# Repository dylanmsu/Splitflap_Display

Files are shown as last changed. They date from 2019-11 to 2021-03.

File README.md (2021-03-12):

# Splitflap_Display
software to digtally drive a public splitflap display using arduino. The display is meant do be deployed in a steamtrain station where it reads the data from their server.
This project is still in development and requires major improvements and code cleanup.

## this repository contains:
* arduino library
* kicad schematic and pcb desgin
* basic documentation about the splitflap display modules

## The Arduino compatible Library
The included Arduino compatible library is designed to drive a complete split flap display board with 32 individual modules. There are also methods included to drive the individual split flaps with great control. You can for example call the method:
```c++
splitflaps.flipSegment(int segment);
```
That line of code will flip the segment once. Or if you want more control, there is the method: 
```c++
splitflaps.writeSegment(int segment, int state);
```
It sets the state of the selected h-Bridge. There are (in the future) a bunch of example sketches with different use cases for the library. However, they all require at least one driver PCB to actually drive the split flap modules.

## The driver PCB
The driver PCBs can drive 8 splitflap modules at the same time, for that it uses 4 SN754410NE chips (L293D in version 4) that are driven by two 74HC595 shift registers. One shift registers drives the H-bridges, the other enables the outputs of the 8 H-Bridges so they dont waste unnecessary power. The communication protocol is quite simple. You have two serial data inputs in the input connector, one is to enable the individual H-Bridges (DiE, ClkE, LaE), the other is to drive the individual H-bridges (Di, Clk, La). They can be daisy-chained to drive an infinite number of splitflap modules. <br> To actually drive splitflap modules with it, open the arduino sketch named TestDriver. Connect the splitflap modules solenoid connections to the H-Bridge output pairs. Then connect the serial pins to the arduino pins listed in the sketch. and lastly connect 20v to the Vdd input connector. Upload the sketch, the splitflaps should be working.

* V1: first version, fully made in kicad with through hole components
* V4: latest version, made in EasyEDA with mostly SMD components

## authors
* Dylan Missuwe
* Tijl Desmet

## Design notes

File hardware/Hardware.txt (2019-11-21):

SEEIT SMTRELAY04 Relaismodule
https://www.conrad.be/p/seeit-smtrelay04-relaismodule-095841
€ 10,49 OK

Highlights
Relaiskaart
4 relais-uitgangen
Compatible met 5V boards

Uitvoering
4 relais-uitgangen
Direct aan te sturen via 5V/DC signaal
Schakelspanning/stroom 250 V/AC 10 A
Eenvoudig aan te sluiten via schroefklemmen
Statusweergave via rode LED.

Netgear GS305E-100PES
https://www.coolblue.be/nl/product/831149/netgear-gs305e-100pes.html
39  € OK

EnGenius ENS202EXTv2
Outdoor 2,4GHz 11n Access Point
€ 102,85 OK

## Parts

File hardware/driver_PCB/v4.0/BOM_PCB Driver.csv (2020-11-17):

ID | Name | Designator | Footprint | Quantity | Manufacturer Part | Manufacturer | Supplier | Supplier Part | LCSC Assembly
1 | CD4049UBDR | U1,U2 | SOIC-16_L9.9-W3.9-P1.27-LS6.0-BL | 2 | CD4049UBDR | TI | LCSC | C22429 | Yes
2 | 100uF | C10,C9,C12,C11 | CAP-TH_BD6.3-P2.50-D1.0-FD | 4 | 100uF 35V 6.3*11 | ValuePro | LCSC | C19504
3 | 10uF | C5,C2,C3,C4,C8,C6,C7,C1 | C0805 | 8 | CL21A106KAYNNNE | SAMSUNG | LCSC | C15850 | Yes
4 | 74HC595D,118 | U3,U4 | SOIC-16_L9.9-W3.9-P1.27-LS6.0-BL | 2 | 74HC595D,118 | Nexperia | LCSC | C5947 | Yes
5 | L293DD013TR | U7,U8,U6,U5 | SOP-20_L13.2-W7.8-P1.27-LS10.4-BL | 4 | L293DD013TR | STMicroelectronics | LCSC | C21610 | Yes
6 | WJ127-5.0-4P | J1,J4,J3,J2 | CONN-TH_4P-P5.00_WJ127-5.0-4P | 4 | WJ127-5.0-4P | Ningbo Kangnex Elec | LCSC | C192779
7 | Shenzhen | CN2,CN1 | CONN-TH_12P-P2.54_B-3100R12P-A110 | 2 | B-3100R12P-A110 | Shenzhen Cankemeng | LCSC | C383583
8 | DB104S | D7,D5,D2,D8,D3,D6,D4,D1 | DBS_L8.4-W6.4-P5.10-LS10.2-TL | 8 | DB104S | MDD | LCSC | C38024 | Yes
9 | JL127-50802G01 | U9 | CONN-TH_2P-P5.08_JL127-50802G01 | 1 | JL127-50802G01 | JILN | LCSC | C409161

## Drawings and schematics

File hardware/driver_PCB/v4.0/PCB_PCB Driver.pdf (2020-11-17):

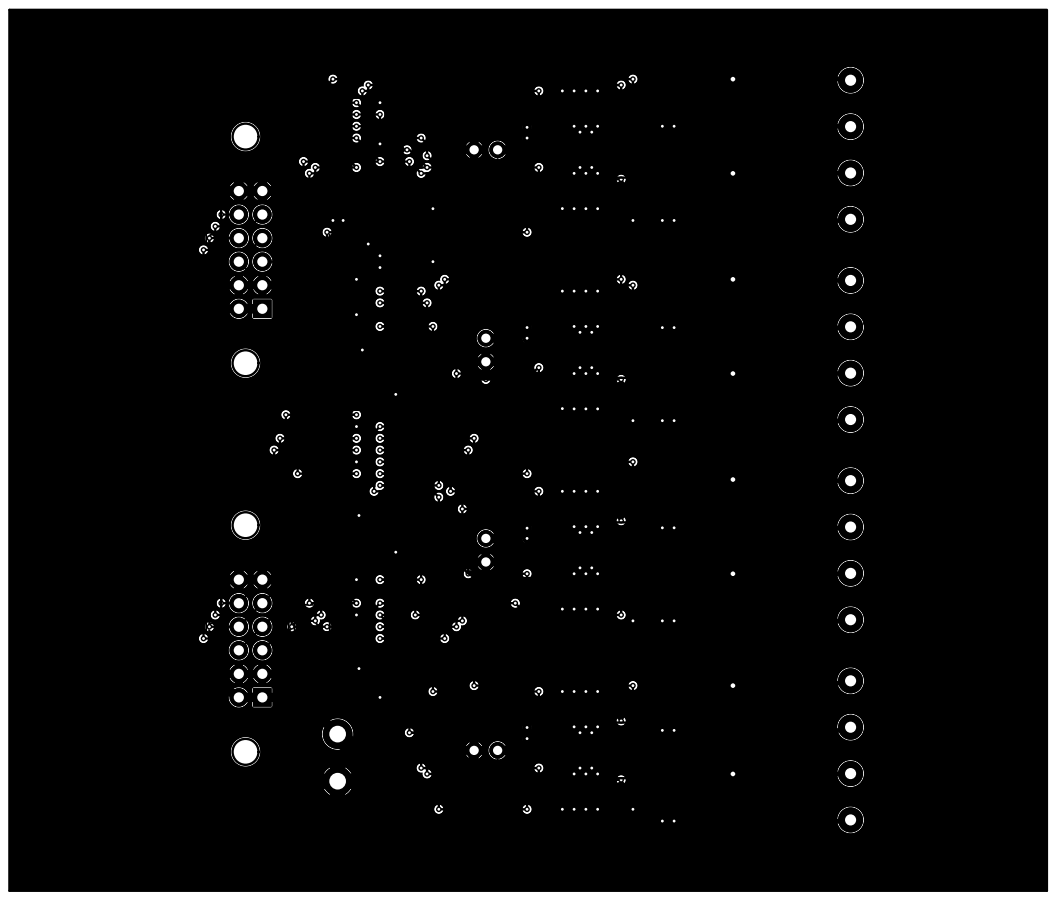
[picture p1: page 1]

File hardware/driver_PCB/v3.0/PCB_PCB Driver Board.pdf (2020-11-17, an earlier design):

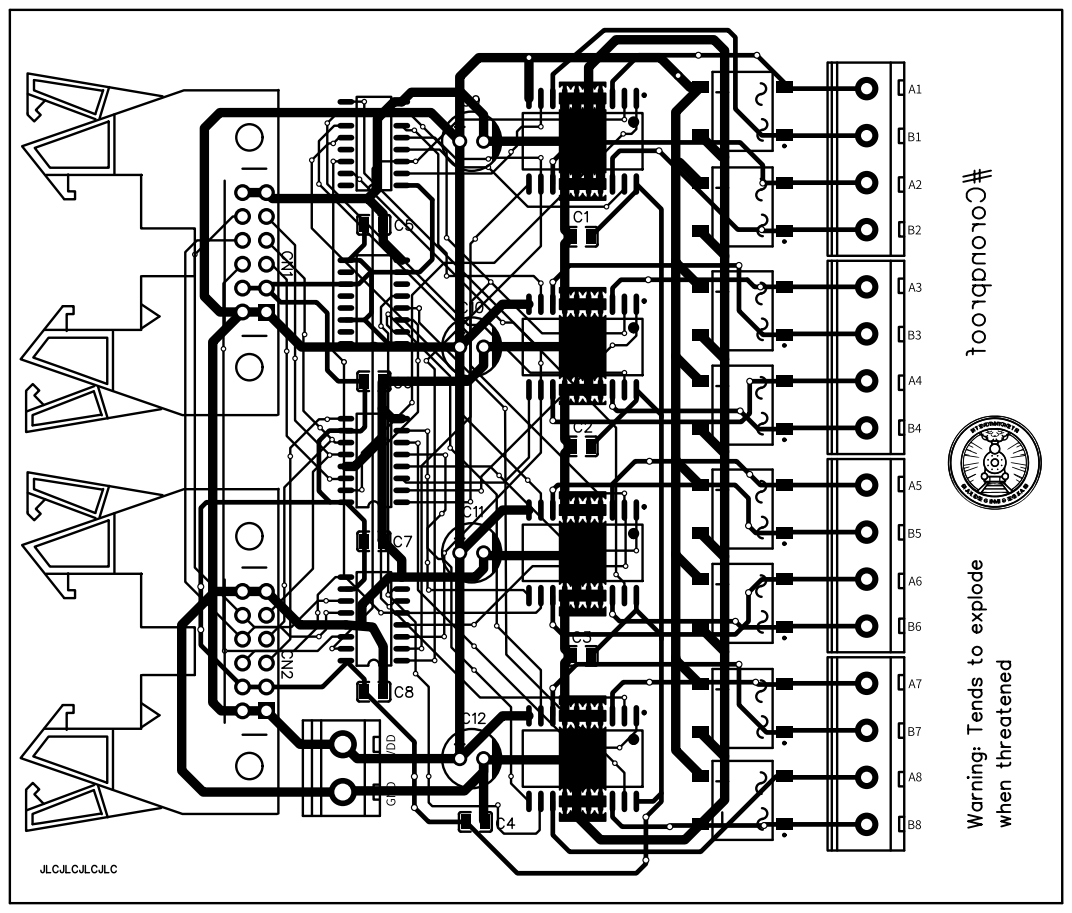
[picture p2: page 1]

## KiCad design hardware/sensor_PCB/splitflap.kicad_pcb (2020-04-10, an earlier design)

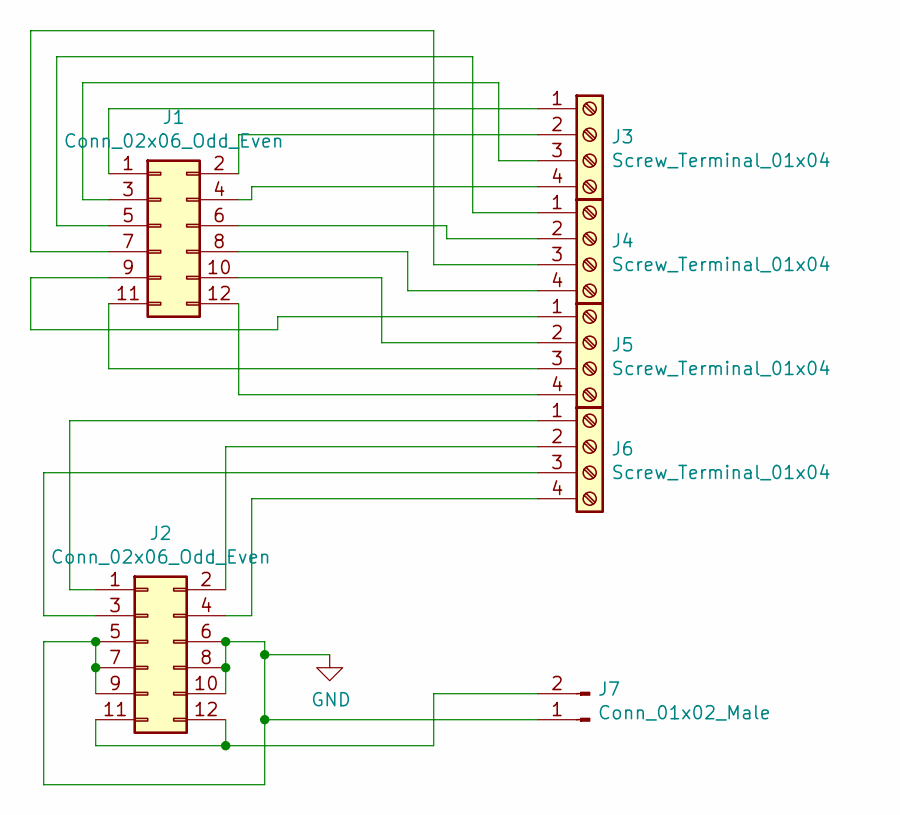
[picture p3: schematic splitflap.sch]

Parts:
J1, J2: Conn_02x06_Odd_Even; IDC-Header_2x06_P2.54mm_Vertical
J3, J4, J5, J6: Screw_Terminal_01x04; TerminalBlock_bornier-4_P5.08mm
J7: Conn_01x02_Male; JST_EH_B2B-EH-A_1x02_P2.50mm_Vertical

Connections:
GND: J2.5, J2.6, J2.7, J2.8, J2.9, J2.10, J7.1
unnamed: J1.1, J3.1
unnamed: J1.2, J3.2
unnamed: J1.3, J3.3
unnamed: J1.4, J3.4
unnamed: J1.5, J4.1
unnamed: J1.6, J4.2
unnamed: J1.7, J4.3
unnamed: J1.8, J4.4
unnamed: J1.9, J5.1
unnamed: J1.10, J5.2
unnamed: J1.11, J5.3
unnamed: J1.12, J5.4
unnamed: J2.1, J6.1
unnamed: J2.2, J6.2
unnamed: J2.3, J6.3
unnamed: J2.4, J6.4
unnamed: J2.11, J2.12, J7.2

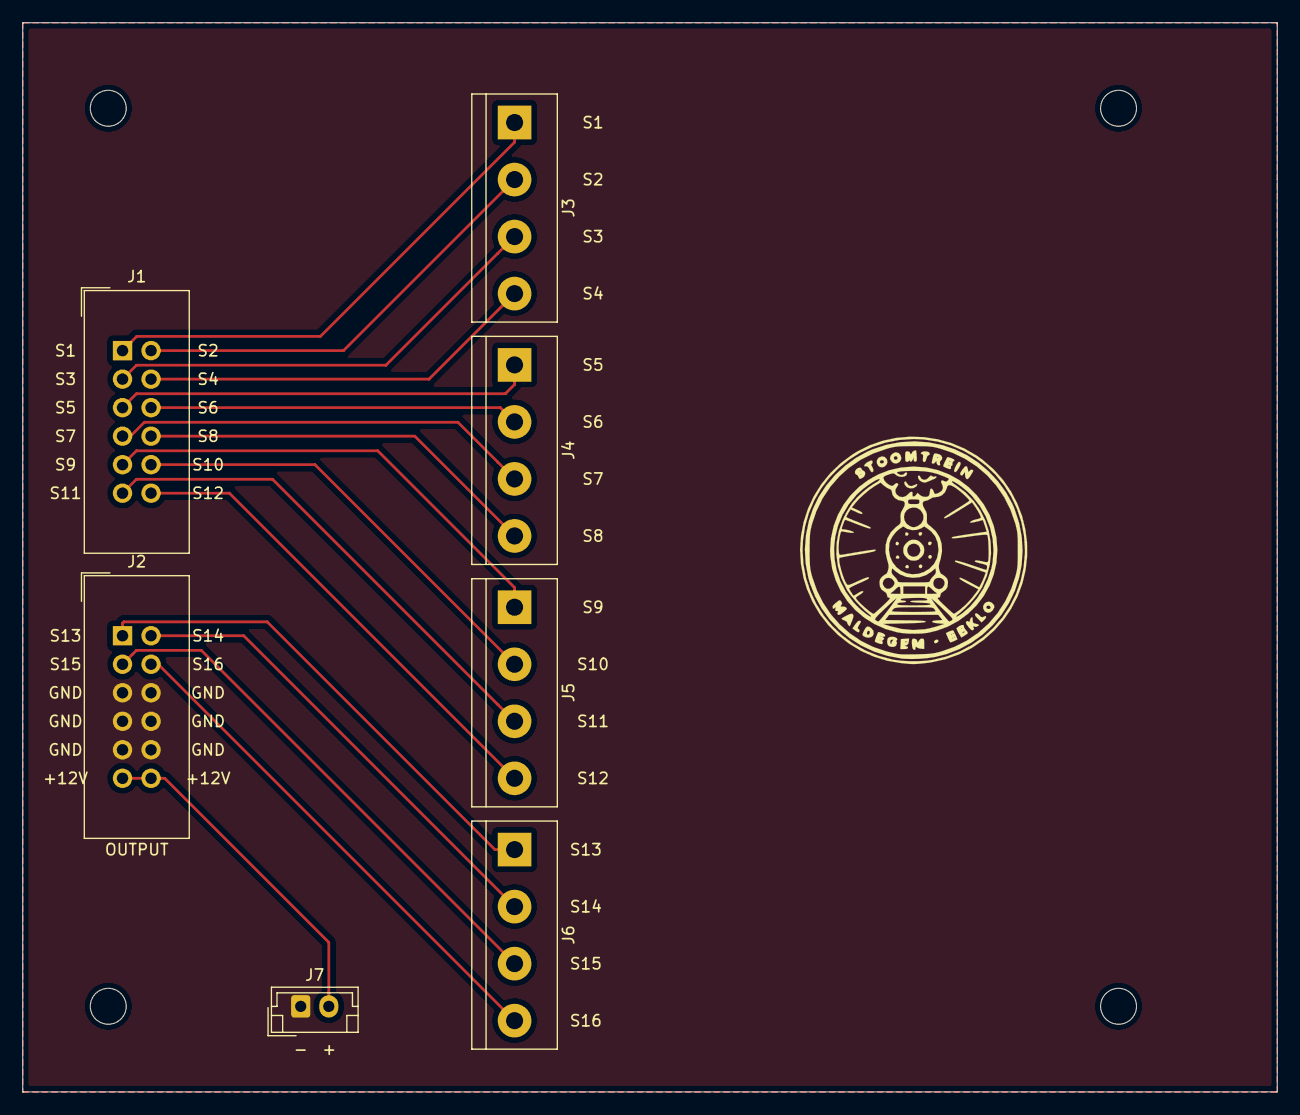
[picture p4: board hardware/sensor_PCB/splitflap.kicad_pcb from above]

Board: 2 copper layers, 111.8 x 95.2 mm, 7 parts (0 on the bottom side), 18 nets.

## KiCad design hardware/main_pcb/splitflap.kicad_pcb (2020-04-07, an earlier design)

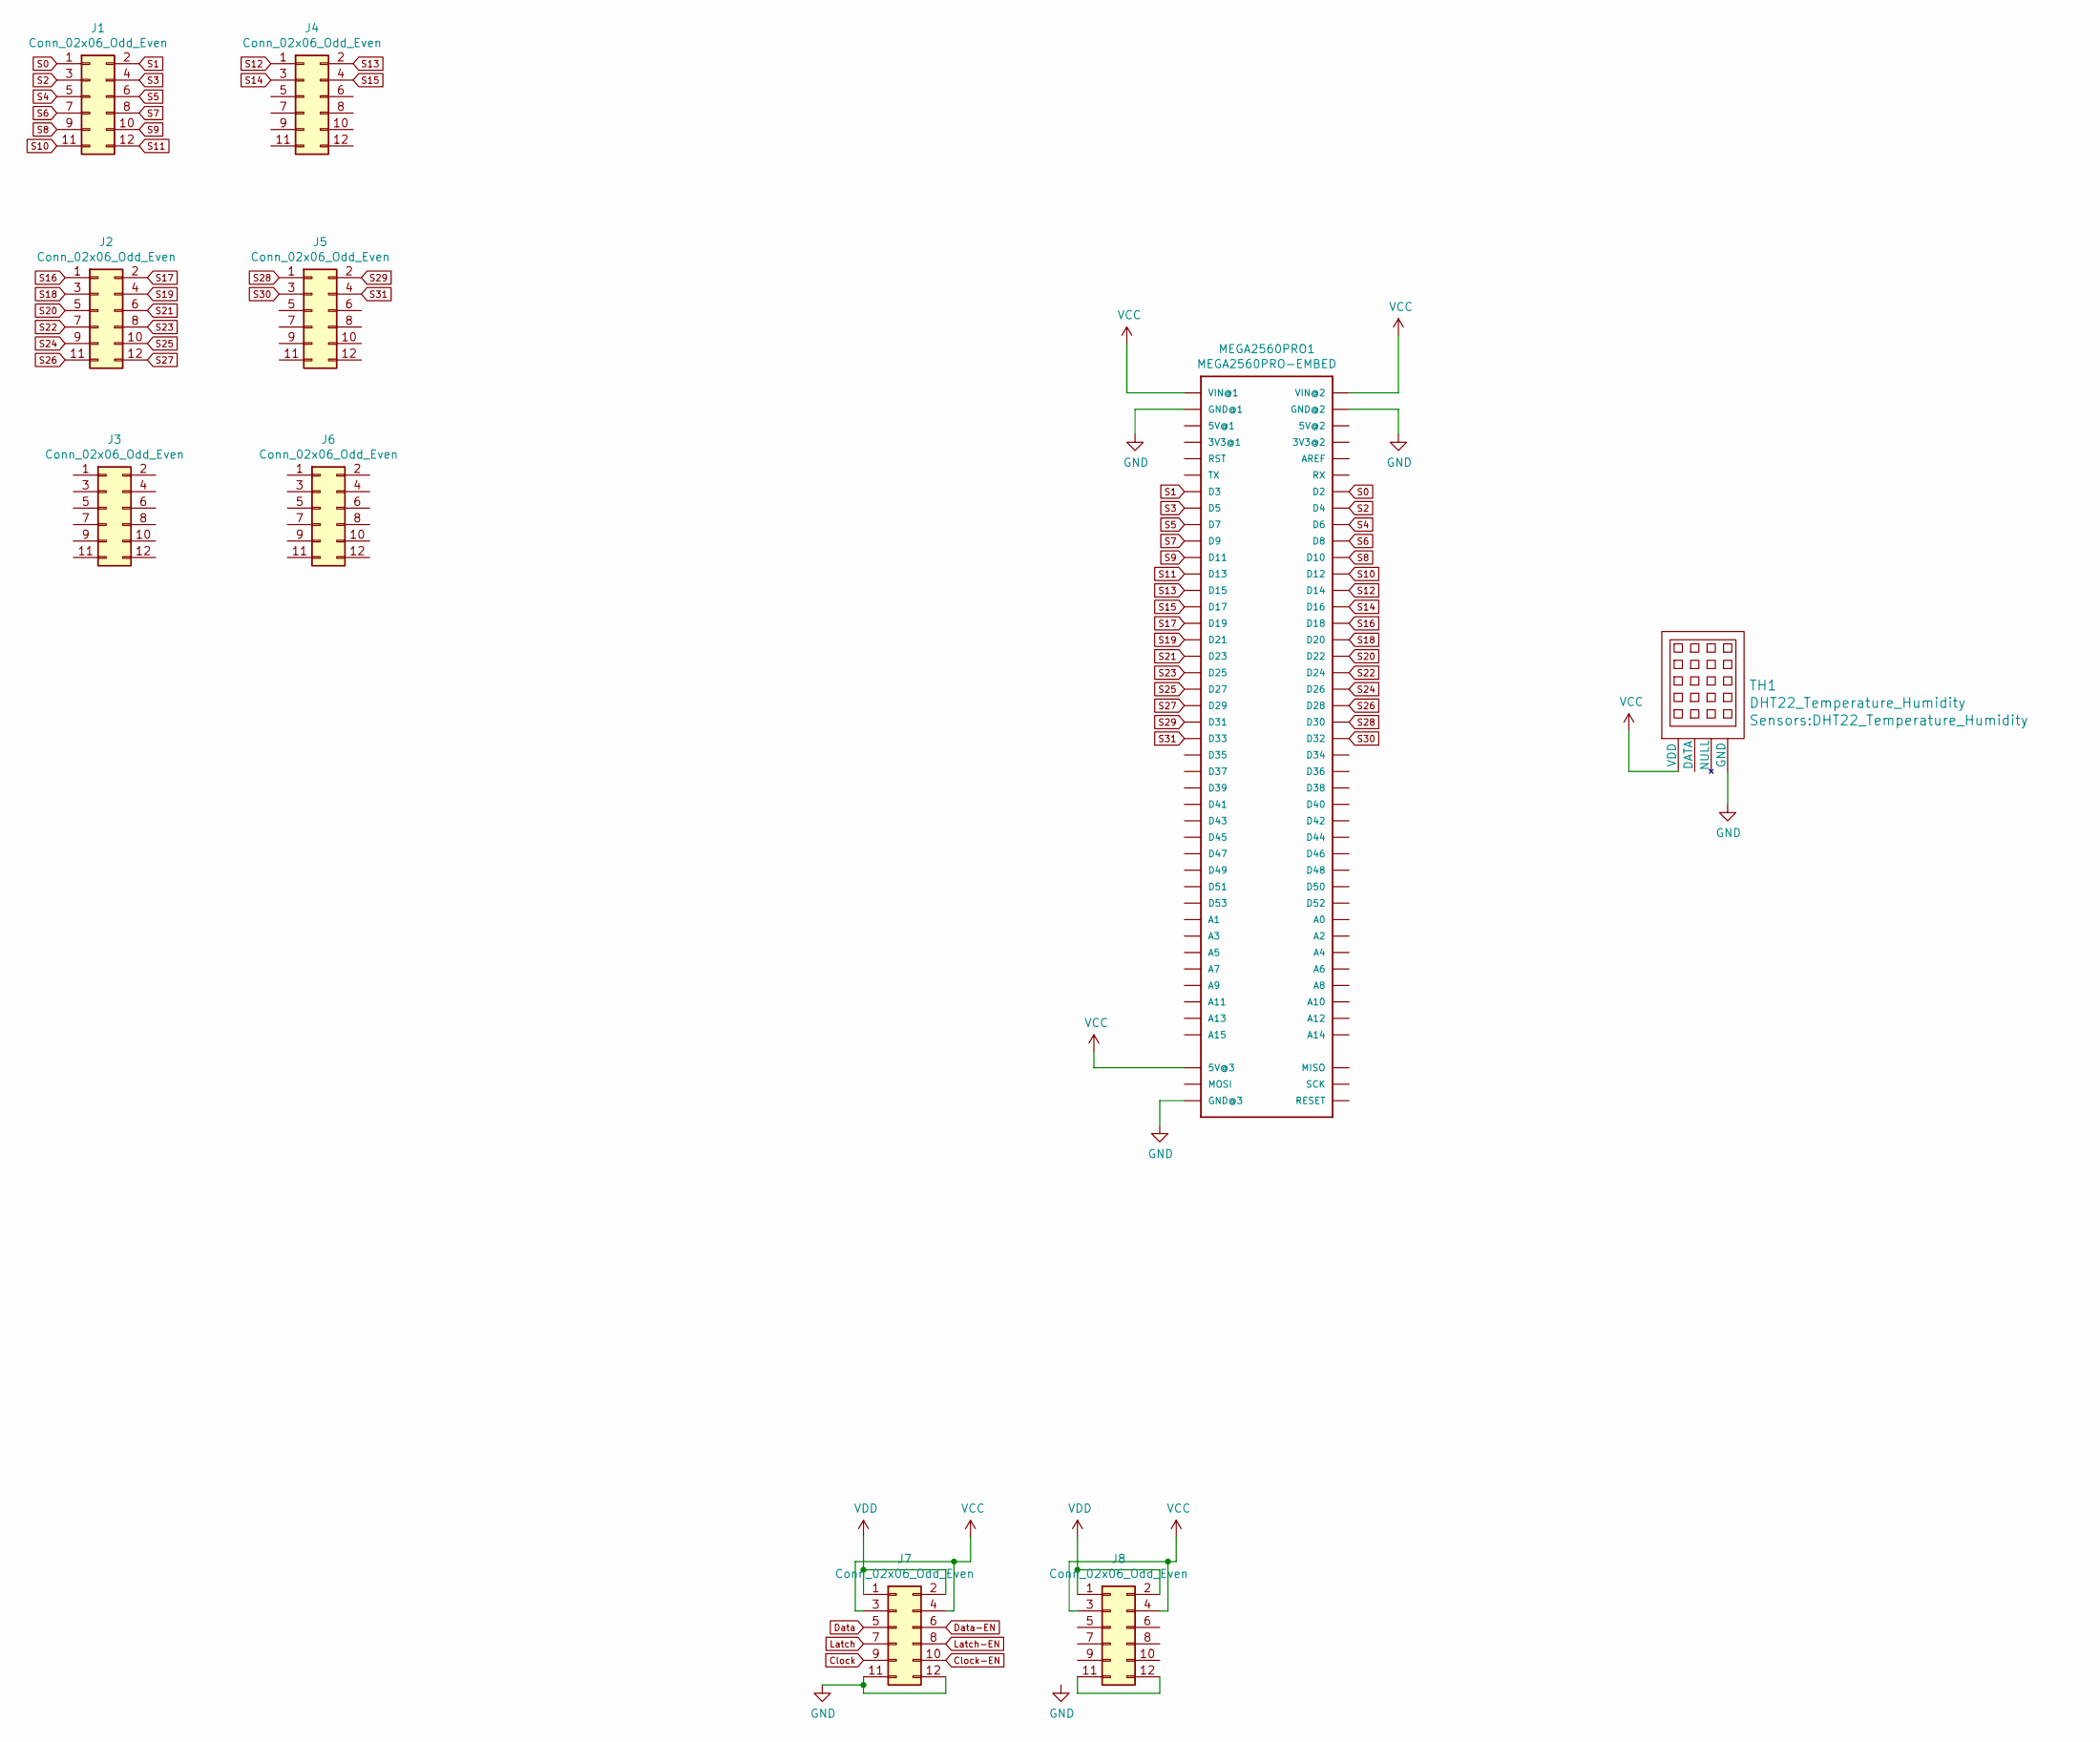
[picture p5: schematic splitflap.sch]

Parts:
J1, J2, J3, J4, J5, J6, J7, J8: Conn_02x06_Odd_Even; IDC-Header_2x06_P2.54mm_Vertical
MEGA2560PRO1: MEGA2560PRO-EMBED
TH1: DHT22_Temperature_Humidity

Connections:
Clock: J7.9
Clock-EN: J7.10
Data: J7.5
Data-EN: J7.6
GND: J7.11, J7.12, MEGA2560PRO1.GND@1, MEGA2560PRO1.GND@2, MEGA2560PRO1.GND@3, TH1.4 (GND)
Latch: J7.7
Latch-EN: J7.8
unnamed: J8.11, J8.12
S0: J1.1, MEGA2560PRO1.D2
S1: J1.2, MEGA2560PRO1.D3
S2: J1.3, MEGA2560PRO1.D4
S3: J1.4, MEGA2560PRO1.D5
S4: J1.5, MEGA2560PRO1.D6
S5: J1.6, MEGA2560PRO1.D7
S6: J1.7, MEGA2560PRO1.D8
S7: J1.8, MEGA2560PRO1.D9
S8: J1.9, MEGA2560PRO1.D10
S9: J1.10, MEGA2560PRO1.D11
S10: J1.11, MEGA2560PRO1.D12
S11: J1.12, MEGA2560PRO1.D13
S12: J4.1, MEGA2560PRO1.D14
S13: J4.2, MEGA2560PRO1.D15
S14: J4.3, MEGA2560PRO1.D16
S15: J4.4, MEGA2560PRO1.D17
S16: J2.1, MEGA2560PRO1.D18
S17: J2.2, MEGA2560PRO1.D19
S18: J2.3, MEGA2560PRO1.D20
S19: J2.4, MEGA2560PRO1.D21
S20: J2.5, MEGA2560PRO1.D22
S21: J2.6, MEGA2560PRO1.D23
S22: J2.7, MEGA2560PRO1.D24
S23: J2.8, MEGA2560PRO1.D25
S24: J2.9, MEGA2560PRO1.D26
S25: J2.10, MEGA2560PRO1.D27
S26: J2.11, MEGA2560PRO1.D28
S27: J2.12, MEGA2560PRO1.D29
S28: J5.1, MEGA2560PRO1.D30
S29: J5.2, MEGA2560PRO1.D31
S30: J5.3, MEGA2560PRO1.D32
S31: J5.4, MEGA2560PRO1.D33
VCC: J7.3, J7.4, J8.3, J8.4, MEGA2560PRO1.5V@3, MEGA2560PRO1.VIN@1, MEGA2560PRO1.VIN@2, TH1.1 (VDD)
VDD: J7.1, J7.2, J8.1, J8.2

Board: 2 copper layers, 10 parts (0 on the bottom side), 36 nets, no tracks yet.

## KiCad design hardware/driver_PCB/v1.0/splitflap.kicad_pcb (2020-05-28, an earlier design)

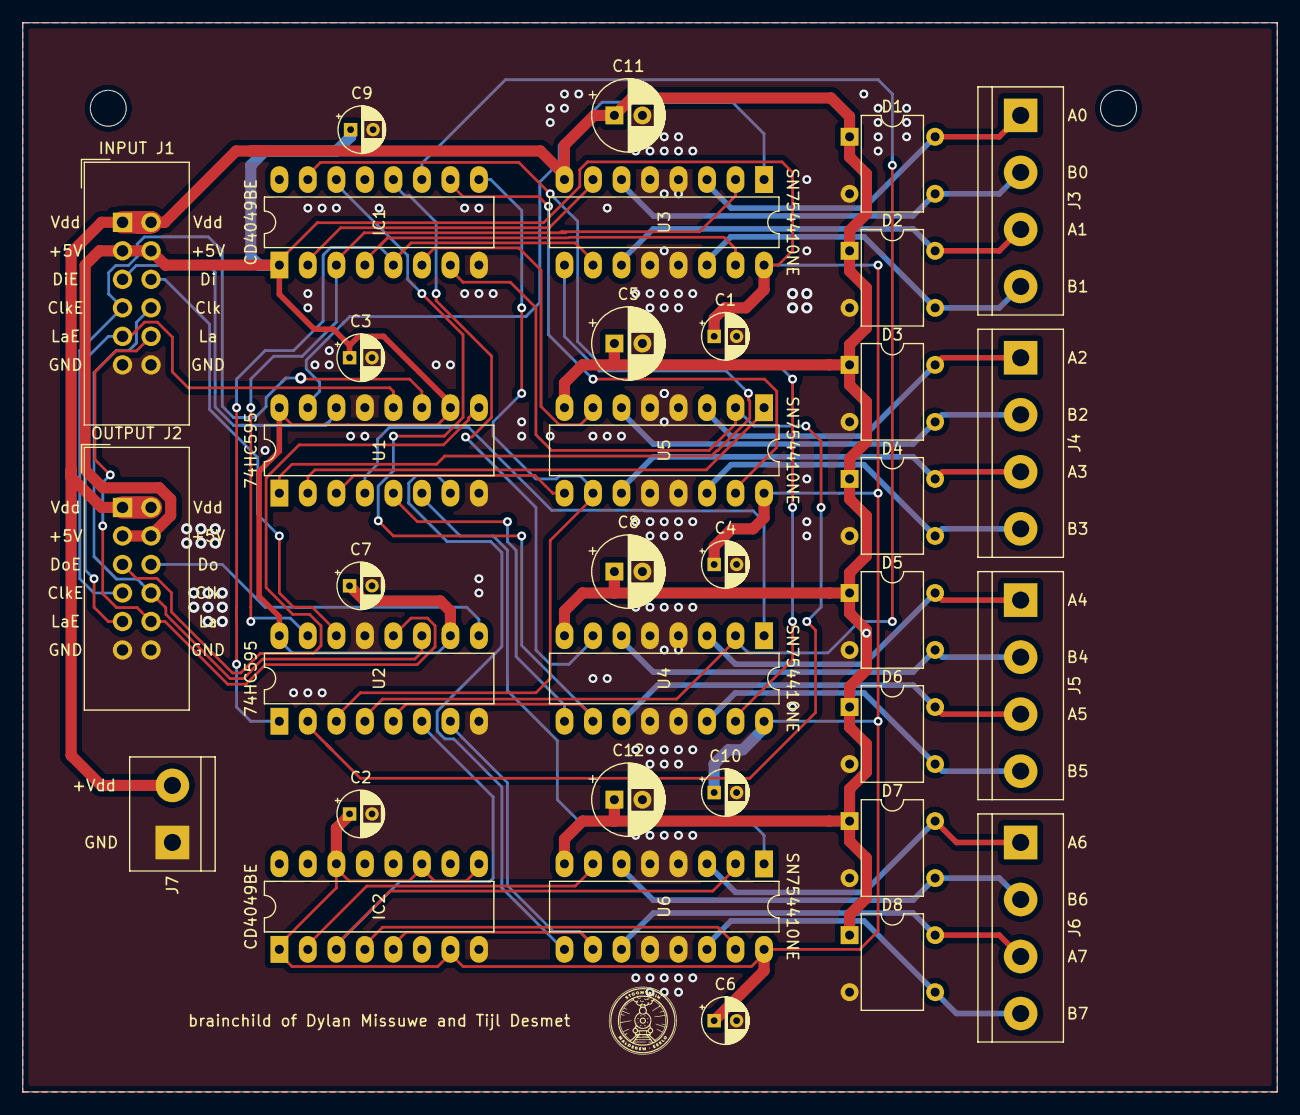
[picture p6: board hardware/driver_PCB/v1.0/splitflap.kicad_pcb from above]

Board: 2 copper layers, 111.8 x 95.2 mm, 35 parts (0 on the bottom side), 51 nets.

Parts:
C1, C2, C3, C4, C6, C7, C9, C10: CP; CP_Radial_D4.0mm_P2.00mm
C5, C8, C11, C12: CP; CP_Radial_D6.3mm_P2.50mm
D1, D2, D3, D4, D5, D6, D7, D8: D_Bridge_+-AA; Diode_Bridge_DIP-4_W7.62mm_P5.08mm
IC1, IC2: CD4049UBE; DIP-16_W7.62mm_LongPads
INPUT J1: Conn_02x06_Odd_Even; IDC-Header_2x06_P2.54mm_Vertical
J3, J4, J5, J6: Screw_Terminal_01x04; TerminalBlock_bornier-4_P5.08mm
J7: Screw_Terminal_01x02; TerminalBlock_bornier-2_P5.08mm
OUTPUT J2: Conn_02x06_Odd_Even; IDC-Header_2x06_P2.54mm_Vertical
U1, U2: 74HC595; DIP-16_W7.62mm_LongPads
U3, U4, U5, U6: SN754410NE; DIP-16_W7.62mm_LongPads

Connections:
GND: C1.2, C2.2, C3.2, C4.2, C5.2, C6.2, C7.2, C8.2, C9.2, C10.2, C11.2, C12.2, D1.2, D2.2, D3.2, D4.2, D5.2, D6.2, D7.2, D8.2, IC1.8, IC2.8, INPUT J1.11, INPUT J1.12, J7.1, OUTPUT J2.11, OUTPUT J2.12, U1.8, U1.13, U2.8, U2.13, U3.4, U3.5, U3.12, U3.13, U4.4, U4.5, U4.12, U4.13, U5.4, U5.5, U5.12, U5.13, U6.4, U6.5, U6.12, U6.13
unnamed: D1.3, J3.2, U3.6
unnamed: D1.4, J3.1, U3.3
unnamed: D2.3, J3.4, U3.14
unnamed: D2.4, J3.3, U3.11
unnamed: D3.3, J4.2, U5.6
unnamed: D3.4, J4.1, U5.3
unnamed: D4.3, J4.4, U5.14
unnamed: D4.4, J4.3, U5.11
unnamed: D5.3, J5.2, U4.6
unnamed: D5.4, J5.1, U4.3
unnamed: D6.3, J5.4, U4.14
unnamed: D6.4, J5.3, U4.11
unnamed: D7.3, J6.2, U6.6
unnamed: D7.4, J6.1, U6.3
unnamed: D8.3, J6.4, U6.14
unnamed: D8.4, J6.3, U6.11
unnamed: IC1.2, U3.7
unnamed: IC1.3, U2.15, U3.2
unnamed: IC1.4, U3.15
unnamed: IC1.5, U2.1, U3.10
unnamed: IC1.6, U5.7
unnamed: IC1.7, U2.2, U5.2
unnamed: IC1.9, U2.3, U5.10
unnamed: IC1.10, U5.15
unnamed: IC1.11, U2.4, U4.2
unnamed: IC1.12, U4.7
unnamed: IC1.14, U2.5, U4.10
unnamed: IC1.15, U4.15
unnamed: IC2.2, U6.7
unnamed: IC2.3, U2.6, U6.2
unnamed: IC2.4, U6.15
unnamed: IC2.5, U2.7, U6.10
unnamed: INPUT J1.5, U1.14
unnamed: INPUT J1.6, U2.14
unnamed: INPUT J1.7, OUTPUT J2.7, U1.11
unnamed: INPUT J1.8, OUTPUT J2.8, U2.11
unnamed: INPUT J1.9, OUTPUT J2.9, U1.12
unnamed: INPUT J1.10, OUTPUT J2.10, U2.12
unnamed: OUTPUT J2.5, U1.9
unnamed: OUTPUT J2.6, U2.9
unnamed: U1.1, U3.9
unnamed: U1.2, U5.1
unnamed: U1.3, U5.9
unnamed: U1.4, U4.1
unnamed: U1.5, U4.9
unnamed: U1.6, U6.1
unnamed: U1.7, U6.9
unnamed: U1.15, U3.1
VCC: C1.1, C2.1, C3.1, C4.1, C6.1, C7.1, C9.1, C10.1, IC1.1, IC2.1, IC2.7, IC2.9, IC2.11, IC2.14, INPUT J1.3, INPUT J1.4, OUTPUT J2.3, OUTPUT J2.4, U1.10, U1.16, U2.10, U2.16, U3.16, U4.16, U5.16, U6.16
VDD: C5.1, C8.1, C11.1, C12.1, D1.1, D2.1, D3.1, D4.1, D5.1, D6.1, D7.1, D8.1, INPUT J1.1, INPUT J1.2, J7.2, OUTPUT J2.1, OUTPUT J2.2, U3.8, U4.8, U5.8, U6.8

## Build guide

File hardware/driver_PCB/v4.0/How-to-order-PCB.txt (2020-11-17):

How to Order PCB

Please refer to:
https://docs.easyeda.com/en/PCB/Order-PCB

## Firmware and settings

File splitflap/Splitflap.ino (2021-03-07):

#include <Ticker.h>
#include <DHT.h>
#include <DHT_U.h>
#include <Adafruit_NeoPixel.h>
#ifdef __AVR__
  #include <avr/power.h>
#endif
#include <Ethernet.h>
#include <SPI.h>

#include "Splitflap.h"
#include "config.h"

// hall-sensor pins from the splitflaps
int sensPins[32] = {
    S0,  S1,  S2,  S3,  S4,  S5,  S6,  S7,
    S8,  S9,  S10, S11, S12, S13, S14, S15,
    S16, S17, S18, S19, S20, S21, S22, S23,
    S24, S25, S26, S27, S28, S29, S30, S31
};

// serial pins of the splitflap driver boards
int serialPins[6] = {
    DATA_ENABLE,
    DATA,
    CLOCK_ENABLE,
    CLOCK,
    LATCH_ENABLE,
    LATCH
};

// variables, they will be changed automatically
double temperature = 0;
double humidity = 0;
double lightLevel = 0;
uint8_t fanSpeed = 0;
uint8_t whiteLED = 0;
uint32_t RGBLedColor = 0;
uint16_t RGBStripMode = 0;
uint16_t RGBStripColor = 0;
String error = "No Error";
String prevtext = "";

void updateDisplay();

Splitflap splitflaps(sensPins, FLAP_DELAY, serialPins);        // make an object from the class
byte mac[] = MAC;      // mac-address of the ethernet module (must be unique)
IPAddress myDns(192, 168, 0, 1);                        // dns server. This is likely your home router
Adafruit_NeoPixel strip = Adafruit_NeoPixel(NUM_RGB_PIXELS, RGB_LED_PIN, NEO_GRB + NEO_KHZ800);
DHT dht(DHT_PIN, DHT22);
EthernetClient client;
Ticker pollTimer(updateDisplay, POLL_DELAY); 

void setup() {
    if (DEBUG) Serial.begin(9600);
    pinMode(LED_R, OUTPUT);
    pinMode(LED_G, OUTPUT);
    pinMode(LED_B, OUTPUT);
    pinMode(LIGHT_SENS, INPUT);
    pinMode(WHITE_LED_EN, OUTPUT);
    pinMode(ENABLE_PS_PIN, OUTPUT);

    pinMode(RGB_STRIP_EN, OUTPUT);
    digitalWrite(RGB_STRIP_EN, 1);
    
    enablePSU();

    strip.begin();
    strip.show();
    strip.setBrightness(RGB_BRIGHTNESS);
    
    initEthernet();
    dht.begin();
    pollTimer.start();

    strip.setPixelColor(10, 255);
}

void loop() {
    pollTimer.update();
    //showAllCharakters();
    //§printSensorStatus();
}

String CombineText(String textA, String textB, String align){
    String text = "";
    if (align == "left"){
        String a = textA + fill(14-textA.length());
        String b = textB + fill(14-textB.length());
        text = a + b;
    } else if (align == "center"){
        String spaceA = fill((14 - textA.length())/2);
        String spaceB = fill((14 - textB.length())/2);
        String a = spaceA + textA + fill(14-(spaceA.length()+textA.length()));
        String b = spaceB + textB + fill(14-(spaceB.length()+textB.length()));
        text = a + b;
    } else if (align == "right"){
        String a = fill(14-textA.length()) + textA;
        String b = fill(14-textB.length()) + textB;
        text = a + b;
    } else {
        if (DEBUG) Serial.println("unrecognized alignment");
    }
    return text;
}

void updateDisplay(){
    
    DynamicJsonDocument doc = fetchFromApi();
    if (DEBUG) Serial.println(doc[BOARD].as<String>());
    if (doc[BOARD].as<String>() != "null") {
        String textA = doc[BOARD]["first_text"].as<String>();
        String textB = doc[BOARD]["second_text"].as<String>();
        String align = doc[BOARD]["align"].as<String>();
        int minutes = doc[BOARD]["minutes"].as<int>();
        int hours = doc[BOARD]["hours"].as<int>();
        int icon = doc[BOARD]["icon_index"].as<int>();
        whiteLED = doc[BOARD]["white_led"].as<int>();
        String stripColor = doc[BOARD]["rgb_strip"]["color"].as<String>();
        RGBStripMode = doc[BOARD]["rgb_strip"]["mode"].as<int>();

        Serial.println(doc[BOARD]["rgb_strip"]["color"].as<String>());
        RGBStripColor = (int) strtol( &stripColor[1], NULL, 16);
        Serial.println(int( strtol( &stripColor[1], NULL, 16)));

        updatePeripherals();
    
        if (textA == "null") {
            textA = "";
        }
    
        if (textB == "null") {
            textB = "";
        }

        String text = CombineText(textA, textB, align);
    
        if (prevtext != text){
            prevtext = text;
            
            delay(1000);
            if (DEBUG) Serial.println("sending " + text + " to the display... ");
            splitflaps.Send(text, icon, hours, minutes);
            if (DEBUG) Serial.println("done.");
        } else {
            if (DEBUG) Serial.println("nothing new to display");
        }
    } else {
        if (prevtext != "no trains"){ 
            prevtext = "no trains";
            splitflaps.Send(fill(28),0,-1,-1);
        }
    }
    pollTimer.start();
}

void updateVariables(){
    temperature = dht.readTemperature();
    humidity = dht.readHumidity();
    lightLevel = getLightLevel();

    if (temperature < 15){
        fanSpeed = 0;
    } else if (temperature < 20) {
        fanSpeed = 128;
    } else if (temperature > 20) {
        fanSpeed = 255;
    }
}

void updatePeripherals(){
    updateVariables();

    Serial.println(RGBStripColor);
    Serial.println(RGBStripMode);
    UpdateRGBStrip();
    
    analogWrite(FAN, fanSpeed);
    analogWrite(WHITE_LED_EN, whiteLED);
    analogWrite(LED_R, (RGBLedColor & 0xff0000) >> 16);
    analogWrite(LED_G, (RGBLedColor & 0x00ff00) >> 8);
    analogWrite(LED_B, (RGBLedColor & 0x0000ff));
}

void printSensorStatus(){
    for (int i=0; i<32; i++){
        if (DEBUG) Serial.print(digitalRead(sensPins[i]));
    }
    if (DEBUG) Serial.println();
    delay(100);
}

void UpdateRGBStrip(){
    uint8_t red = (RGBStripColor & 0xff0000) >> 16;
    uint8_t grn = (RGBStripColor & 0x00ff00) >> 8;
    uint8_t blu = (RGBStripColor & 0x0000ff);

    switch(RGBStripMode) {
        case 0:
            strip.clear();
            break;
        case 1:
            strip.fill(strip.Color(red, grn, blu), 0, NUM_RGB_PIXELS);
            break;
        
    }
}

int getLightLevel(){
    return analogRead(LIGHT_SENS);
}

void enablePSU() {
    digitalWrite(ENABLE_PS_PIN, LOW);
}

void disablePSU() {
    digitalWrite(ENABLE_PS_PIN, HIGH);
}

void RGBLed(int r, int g, int b){
    RGBLedColor = (r << 16) || (g << 8) || (b);
}

void showAllCharakters(){
    String alphabet = "abcdefghijklmnopqrstuvwxyz-_/ ABCDEFGHIJKLMNOPQRSTUVWXYZ?";
    for (int i=0; i<58; i++){
        
        String text = "";
        for (int j=0; j<28; j++){
            text += String(alphabet[i]);
        }

        Serial.print("showing: ");
        Serial.println(String(text));
        splitflaps.Send(text, 0, 0, 0);
        delay(15000);
    }
}

String fill(int amount){
    String spaces = "";
    for (int i=0; i<amount; i++){
        spaces += " ";
    }
    return spaces;
}

void initEthernet() {
    if (DEBUG) Serial.print("initializing Ethernet... ");
    delay(1000);
    Ethernet.init(53);
    Ethernet.begin(mac);
    delay(2000);
    if (DEBUG) Serial.println("done.");
}

char *stringToCharArray(String string){
    char Array[string.length()];
    string.toCharArray(Array, string.length());
    return Array;
}

DynamicJsonDocument fetchFromApi(){
    if (DEBUG) Serial.println("fetching data from api...");
    if (DEBUG) Serial.print("\tconnecting... ");
    client.setTimeout(1000);
    int numReconnect = 0;
    while (!client.connect(HOSTNAME, 80)){
        numReconnect += 1;
        if (DEBUG) Serial.println(F("\tConnection failed"));
        delay(500);
        if (DEBUG) Serial.println(F("\tTrying again..."));
        delay(1000);
        if (numReconnect >= 10){
            error = "Unable to connect";
            return;
        }
    }

    if (DEBUG) Serial.println("\tconnected!");
    
    // Send HTTP request
    if (DEBUG) Serial.println("\tsending request and awaiting... ");

    client.print("GET ");
    client.print(ROUTE);
    client.println(" HTTP/1.1");

    client.print("Host: ");
    client.println(HOSTNAME);

    client.print("User-Agent: ");
    client.println("arduino-ethernet");
    
    client.print("board: ");
    client.println(BOARD);
    
    client.print("temperature: ");
    client.println(temperature);
    
    client.print("humidity: ");
    client.println(humidity);

    client.print("lightLevel: ");
    client.println(getLightLevel());

    client.print("error: ");
    client.println("No");

    client.print("RGBColor: ");
    client.println("ffffff");
    
    client.print("ledIntensity: ");
    client.println("255");


    /*client.println("GET /index.php HTTP/1.1");
    client.println("Host: api.scm-team.be");
    client.println("board: A");
    client.println("temperature: 19");
    client.println("humidity: 0");
    client.println("lightLevel: 500");
    
    client.println("error: No");
    client.println("RGBColor: ffffff");
    client.println("ledIntensity: 255");*/
    
    client.println("Connection: close");
    if (client.println() == 0) {
        if (DEBUG) Serial.println(F("Failed to send request"));
        return;
    } else {
        if (DEBUG) Serial.println("done.");
    }
    
    // Check HTTP status
    char status[32] = {0};
    client.readBytesUntil('\r', status, sizeof(status));
    if (strcmp(status, "HTTP/1.1 200 OK") != 0) {
        if (DEBUG) Serial.print(F("\tUnexpected response: "));
        if (DEBUG) Serial.println(status);
        return;
    } else {
        if (DEBUG) Serial.println("\tstatus: 200 OK");
    }
    
    // Skip HTTP headers
    char endOfHeaders[] = "\r\n\r\n";
    if (!client.find(endOfHeaders)) {
        if (DEBUG) Serial.println(F("\tInvalid response"));
        return;
    }

    // Allocate the JSON document
    // Use arduinojson.org/v6/assistant to compute the capacity.
    if (DEBUG) Serial.print("\tparsing json data... ");
    const size_t capacity = JSON_OBJECT_SIZE(20) + JSON_ARRAY_SIZE(2) + 500;
    DynamicJsonDocument doc(capacity);

    // Parse JSON object
    DeserializationError error = deserializeJson(doc, client);
    if (error) {
        if (DEBUG) Serial.print(F("\tdeserializeJson() failed: "));
        if (DEBUG) Serial.println(error.c_str());
        return;
    }
    if (DEBUG) Serial.println("done.");
    return doc;
}

void rainbowCycle(uint8_t wait) {
    uint16_t i, j;
    
    for(j=0; j<256*5; j++) { // 5 cycles of all colors on wheel
        for(i=0; i< strip.numPixels(); i++) {
          strip.setPixelColor(i, Wheel(((i * 256 / strip.numPixels()) + j) & 255));
        }
        strip.show();
        delay(wait);
    }
}

uint32_t Wheel(byte WheelPos) {
    WheelPos = 255 - WheelPos;
    if(WheelPos < 85) {
        return strip.Color(255 - WheelPos * 3, 0, WheelPos * 3);
    }
    if(WheelPos < 170) {
        WheelPos -= 85;
        return strip.Color(0, WheelPos * 3, 255 - WheelPos * 3);
    }
    WheelPos -= 170;
    return strip.Color(WheelPos * 3, 255 - WheelPos * 3, 0);
}

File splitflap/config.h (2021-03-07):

// parameters
#define BOARD           "B"
#define DEBUG           true
#define FLAP_DELAY      150 //ms
#define POLL_DELAY      10000 //ms
#define NUM_RGB_PIXELS  144
#define RGB_BRIGHTNESS  128

// network
#define HOSTNAME        "api.scm-team.be"
#define ROUTE           "/index.php"
#define PORT            80
#define MAC             {0xDE, 0xAD, 0xBE, 0xEF, 0xFE, 0xEB}

// pins
#define RGB_LED_PIN     47
#define RGB_STRIP_EN    46
#define ENABLE_PS_PIN   35
#define DHT_PIN         49
#define WHITE_LED_EN    45
#define FAN             2
#define LIGHT_SENS      A0

#define LED_R           3
#define LED_G           4
#define LED_B           5

#define STAT_A          6
#define STAT_B          7
#define STAT_C          8

#define DATA_ENABLE     44
#define DATA            38
#define CLOCK_ENABLE    42
#define CLOCK           36
#define LATCH_ENABLE    40
#define LATCH           34

// sensor pins
#define S0              15
#define S1              16
#define S2              17
#define S3              18
#define S4              19
#define S5              22
#define S6              23
#define S7              24
#define S8              25
#define S9              26
#define S10             27
#define S11             28
#define S12             29
#define S13             30
#define S14             31
#define S15             A1
#define S16             A2
#define S17             A3
#define S18             A4
#define S19             A5
#define S20             A6
#define S21             A7
#define S22             A8
#define S23             A9
#define S24             A10
#define S25             A11
#define S26             A12
#define S27             A13
#define S28             A14
#define S29             A15
#define S30             32
#define S31             33

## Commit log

2019-11-01 created arduino file
2019-11-03 got the code to print 'hello' on actual hardware
2019-11-09 added sensor functionality
2019-11-11 Added LED functionality
2019-12-06 added kicad schematic
    [splitflap.kicad_pcb, splitflap.sch]
2019-12-07 updated kicad schematic
    [splitflap.kicad_pcb, splitflap.sch]
2019-12-07 updated pcb layout
    [splitflap.kicad_pcb]
2020-01-23 finished pcb layout
    [splitflap-B_Cu.gbr, splitflap-B_Mask.gbr, splitflap-B_Paste.gbr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]
2020-02-22 changed pcb layout and interface
    [splitflap.kicad_pcb, splitflap.sch]
2020-02-23 added functionality to read from serial
    [_saved_splitflap.sch]
2020-02-24 some code cleanup
    [_saved_splitflap.sch]
2020-03-10 updated pcb
    [splitflap.kicad_pcb]
2020-04-07 converted arduino sketch to a library ann pcb updates
    [splitflap-B_Cu.gbr, splitflap-B_Mask.gbr, splitflap-B_Paste.gbr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]
2020-04-10 updated splitflap library
    [splitflap.kicad_pcb, splitflap.sch]
2020-05-28 Dylan wist het niet meer
2020-11-03 added PCB layout
    [BOM_Driver Board.csv, BOM_PCB Driver.csv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]
2020-11-05 Changes to character list
    [Character List.xlsx]
2020-11-05 General changes for mental wellbeing
    [Character List.xlsx]
2020-11-05 Added Documentation
    [Character List.xlsx]
2020-11-06 Minor changes
    [Character List.xlsx]
2021-01-03 added drivertest example
    [PSU_pcb.kicad_pcb, PSU_pcb.sch, test.kicad_pcb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]
2021-01-03 moved charakter list to documentation
    [Character List.xlsx]
